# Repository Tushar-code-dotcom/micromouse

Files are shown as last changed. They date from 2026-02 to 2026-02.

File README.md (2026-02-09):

# micromouse

This repository consists of my PCB design of the micromouse robot. 
You can see the schematic and the layout pdf for quick glance.

To download the kicad files navigate to `schematic-layout-files` directory.

The micromouse is one of the oldest robotics race.
The goal is simple: get to the end of the maze as fast as possible.

This is actually my first prototype PCB for the robot, At the time of writing- I have soldered the components, including the buck converter SMPS circuit. I am using a 12V battery to power the robot. The buck converter circuit did not work, one of the possible cause- according to my limited knowledge right now, could be the use of 470uF aluminum capacitor as opposed to the recommended 680-2000uF aluminum capacitor.

The datasheet had recommened that the output capacitor can be between 100uF to 470uF if it is a tantalum capacitor.
If an aluminium capacitor were to be chosen, it had to be in between 680uF-2000uF.
According to the datasheet, 
```
Tantalum capacitors can have a very low ESR, and must be carefully evaluated if it is the only output capacitor
```
And the ESR matters, because 

```
Output Ripple Voltage = (∆IIND) (ESR of COUT) 
```
Lesser the ESR of the output capacitor, lesser would be output ripple voltage, stabler would be the output
Further analysis must be carried out to analyze the fault and determine what is the cause of no output at the buck circuit.

Components used in the micromouse are-

<table><thead>
  <tr>
    <th>STM32F407VGT6</th>
    <th>Main microcontroller</th>
  </tr></thead>
<tbody>
  <tr>
    <td>N20 600 RPM Micro-Metal gear motor</td>
    <td>Motor for driving the robot</td>
  </tr>
  <tr>
    <td>LM2576 5V Output SMPS Switcher IC- HTC   Korea</td>
    <td>Stepping down voltage from 12V to 5V</td>
  </tr>
  <tr>
    <td>AMS 1117 3.3V LDO</td>
    <td>Stepping down voltage from 12V to 5V</td>
  </tr>
  <tr>
    <td>HM-BT4502 bluetooth module</td>
    <td>For wirelessly receiving data from the uC</td>
  </tr>
  <tr>
    <td>IR   Emitter/Receiver pair(could be replaced with more accurate and cheaper mmWave   radar)</td>
    <td>For sensing the distance from the walls</td>
  </tr>
  <tr>
    <td>12V Li-ion battery</td>
    <td>For powering the robot</td>
  </tr>
</tbody>
</table>

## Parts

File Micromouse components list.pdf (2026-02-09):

# Micromouse components list

1. H bridge- https://evelta.com/h-bridge-motor-driver-ic-1.5a-sop-8/ H bridge motor driver IC SOP-8 Datasheet- https://evelta.com/content/datasheets/359-BL5612.pdf
2. Motor- # GA12-N20 12V 1000RPM Micro DC Metal Gear Reduction Motorhttps://zbotic.in/product/ga12-n20-12v-1000rpm-micro-dc-metal-gear-reduction-motor/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 (https://zbotic.in/product/ga12-n20-12v-1000rpm-micro-dc-metal-gear-reduction-motor/?gad_source=1) datasheet-
3. Motor with encoder 500 rpm gear ratio 30:1 rated current 40mA, stall current 1A--https://robokits.co.in/motors/n20-metal-gear-micro-motors/n20-metal-gear-encodermotor/ga12-n20-6v-500-rpm-all-metal-gear-micro-dc-encoder-motor-with-precious-metalbr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
srsltid=AfmBOop46_ggaORufaxEpk0p9WgjGFxgG4g6K782mz7oQ7eS4OKStQTLCls&gQT =2 (https://robokits.co.in/motors/n20-metal-gear-micro-motors/n20-metal-gear-encoder-motor/ga12-n20-6v-500-rpm-all-metal-gear-micro-dc-encoder-motor-with-precious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)
4. https://robu.in/product/ir-receiver-diode-tsop38238/?gQT=1 receiver
5. IR Emitter datasheet- https://cdn-shop.adafruit.com/datasheets/IR333_A_datasheet.pdf
6. TCRT5000 IR EMITTER/RECEIVER PAIR- https://robu.in/wp-content/uploads/2022/09/Vishay-TCRT5000L-datasheet.pdf (https://robu.in/wp-content/uploads/2022/09/Vishay-TCRT5000L-datasheet.pdf)
7. 3 way Dipswitch- https://evelta.com/dip-switch-3-way-slide-type-red-ds-03r/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 (https://evelta.com/dip-switch-3-way-slide-type-red-ds-03r/?gad_source=1) Datasheet- https://evelta.com/content/datasheets/408-DS-Series.pdf
8. Pushbutton- https://sharvielectronics.com/product/tactile-push-button-switch-12x12x7-3mm/
9. motor for propeller- https://robu.in/product/65mm-blade-propeller-prop-8520-cw-ccwcoreless-brushed-motor-indoor-racing-drone-quad-copter/ (https://robu.in/product/65mm-blade-propeller-prop-8520-cw-ccw-coreless-brushed-motor-indoor-racing-drone-quad-copter/) (3.7V)
10. 12V battery- https://quartzcomponents.com/products/12v-1200mah-rechargeable-lithiumbattery-with-warranty-for-gps-cctv-industial-and-commercial-application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¤cy=INR&utm_medium=product_sync&utm_source=google&utm_content=sag_organic&utm_campaign=sag_organic?utm_source=google&utm_medium=FreeListings&gad_source=1&gclid=Cj0KCQiAhbi8BhDI ARIsAJLOlud7CVXVUGHuGk0HCnHtH1EE9qVLhCeel78XtQ66bBOLSDcrkV2ftdoaAkUKE ALw_wcB (https://quartzcomponents.com/products/12v-1200mah-rechargeable-lithium-battery-with-warranty-for-gps-cctv-industial-and-commercial-application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)
11. 2.4V 1000RPM (30mA to 60mA continuous current) DC motor with encderhttps://robu.in/product/n12-2-4v-1200rpm-metal-gear-motor-with-encoder/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 (https://robu.in/product/n12-2-4v-1200rpm-metal-gear-motor-with-encoder/?gad_source=1)

12. If 12V motor used, then motor driver- https://evelta.com/content/datasheets/035-DRV8212PDSGR.pdf (https://evelta.com/content/datasheets/035-DRV8212PDSGR.pdf)
13. 5V 1000rpm motor- https://robu.in/product/n12-5v-1200rpm-metal-gear-motor-with-encoder/datsheet- https://robu.in/wp-content/uploads/2023/09/9-GM12-N20VA.pdf
14. propellers- https://robu.in/product/orange-hd-1209-31mm-pc-4-blade-0-8mm-propellers-4cw4ccw-clear-gray/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 (https://robu.in/product/orange-hd-1209-31mm-pc-4-blade-0-8mm-propellers-4cw4ccw-clear-gray/?gad_source=1) alternative linkhttps://evelta.com/gemfan-31mm-1209-4-blade-propeller-1-5mm/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 (https://evelta.com/gemfan-31mm-1209-4-blade-propeller-1-5mm/?gad_source=1)
15. stm32f401ret6 micrcontroller LQFP64- https://robu.in/product/stm32f401ret6-stmicroelectronics-arm-mcu-dynamic-efficiency-line-stm32-family-stm32f4-seriesmicrocontrollers-arm-cortex-m4/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 (https://robu.in/product/stm32f401ret6-stmicroelectronics-arm-mcu-dynamic-efficiency-line-stm32-family-stm32f4-series-microcontrollers-arm-cortex-m4/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)
16.

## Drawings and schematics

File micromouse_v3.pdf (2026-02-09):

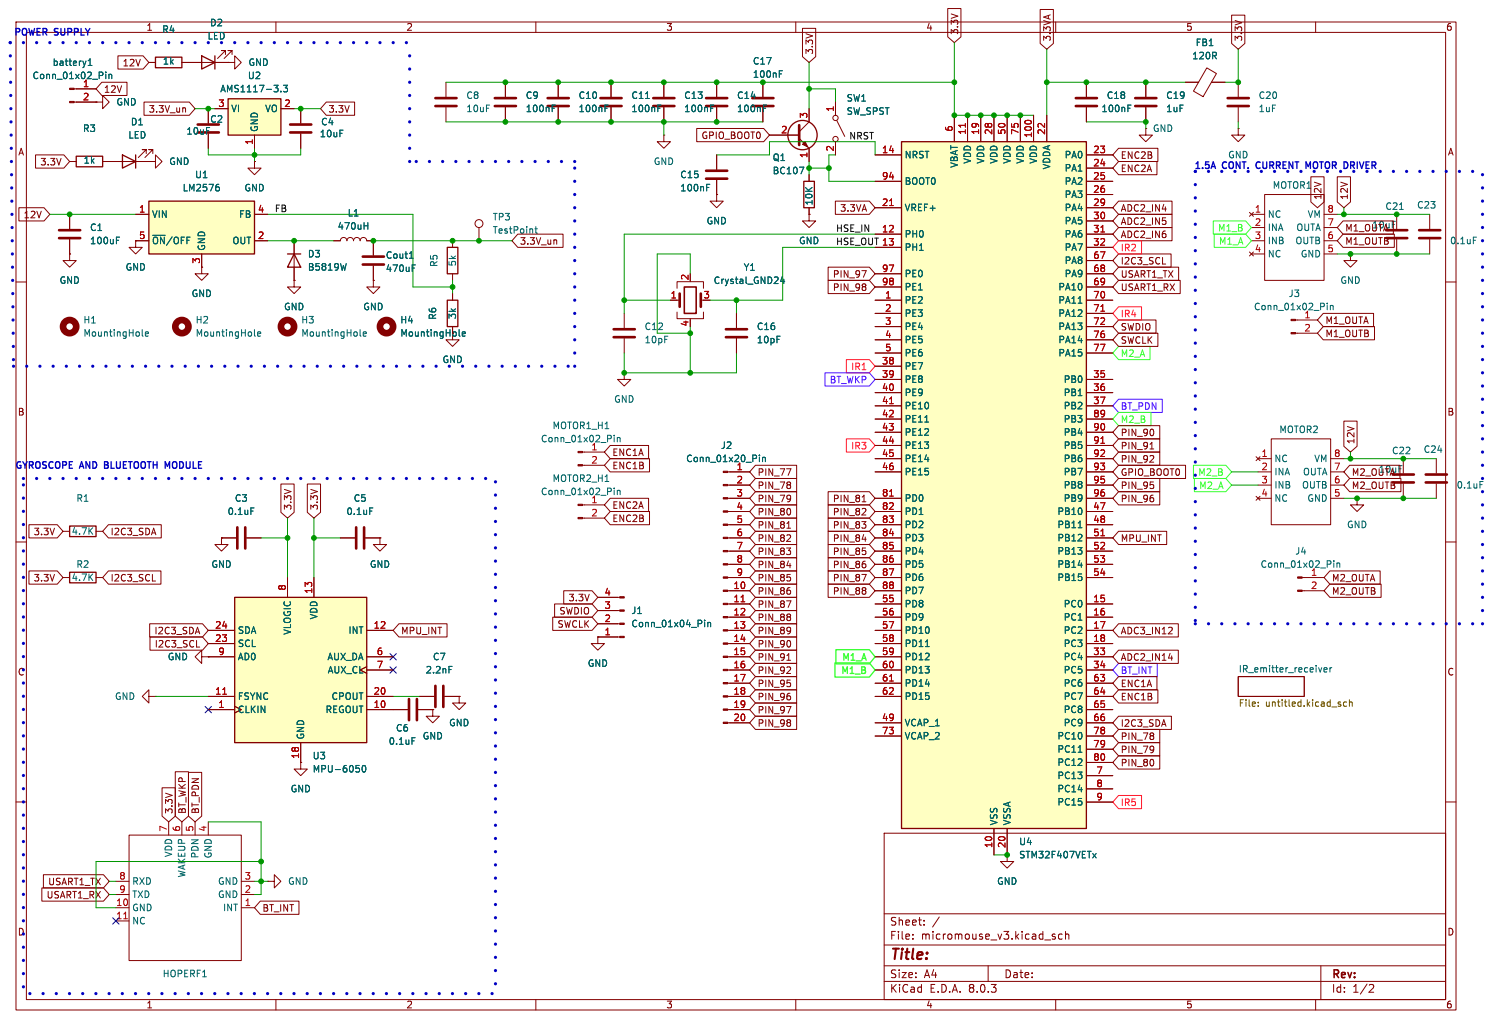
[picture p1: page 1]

3 FB 4 ~{ON}/OFF 5 U2 AMS1117-3.3 GND

1.5A CONT. CURRENT MOTOR DRIVER GYROSCOPE AND BLUETOOTH MODULE

Id: 1/2 Title: File: micromouse_v3.kicad_sch Sheet: /

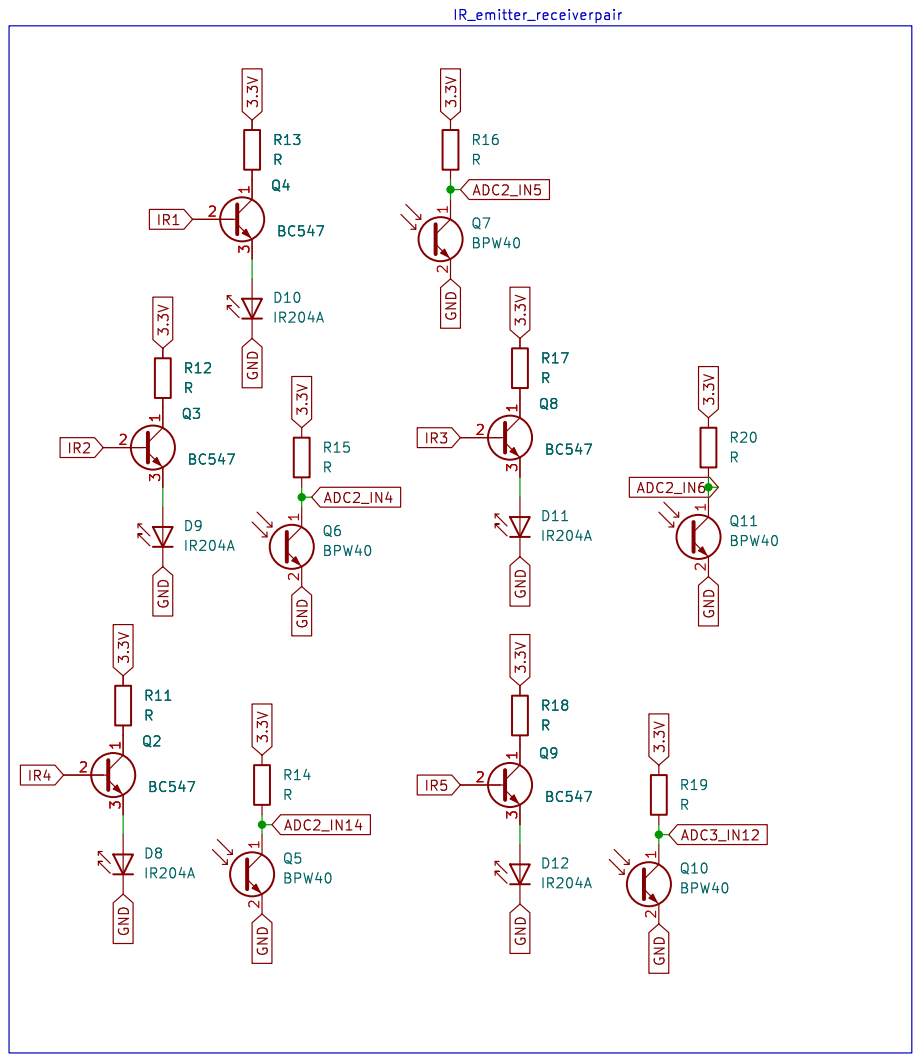
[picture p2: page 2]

Id: 2/2 Title: File: untitled.kicad_sch Sheet: /IR_emitter_receiver/ R14 R

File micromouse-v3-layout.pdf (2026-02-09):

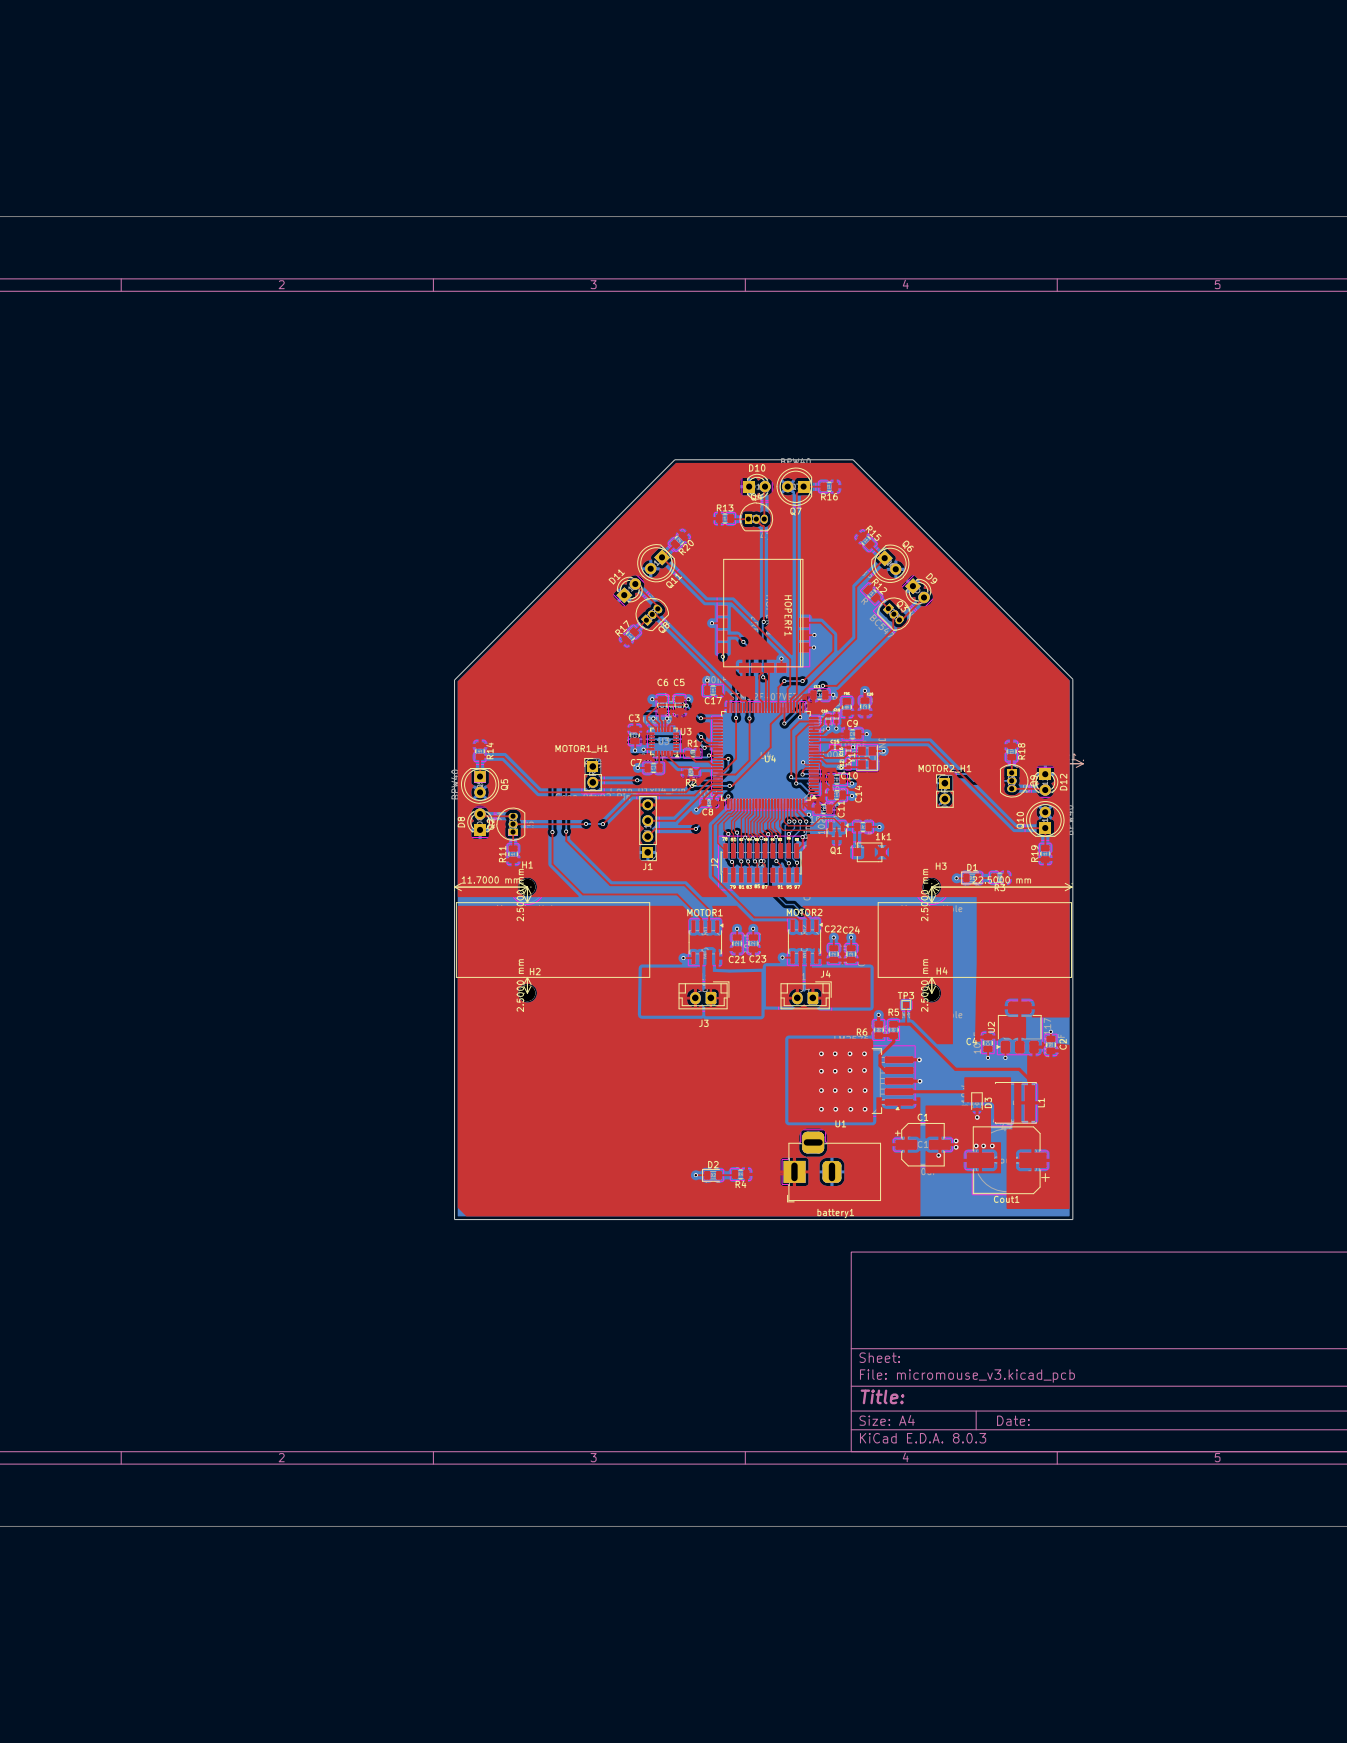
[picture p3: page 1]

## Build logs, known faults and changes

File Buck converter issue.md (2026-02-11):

I am not sure which of these issue could be the root cause of my DC-DC step down converter not working so I will list them one by one

### 1. Soldering at a higher temperature

I have soldered the buck converter, with a hot air gun at a temperature of 350 degree celsius for roughly 30 seconds-1 minute, I have resorted to such high temperatures, because a considerable amount of solder had to be melted before placing the IC on the PCB

![[Pasted image 20260210220326.png]]

![[WhatsApp Image 2026-02-10 at 10.07.25 PM.jpeg]]

#### **The issue**
Maybe the exposure to such temperature(350 deg C) could have caused the IC, to not work at all, because I was getting no input at the feedback pin

![[Pasted image 20260210225434.png]]
### 2. Using LTSpice model of TI instead of HTC korea to simulate
Maybe this is a bigger blunder considering that I have bought an HTC LM2576 regulator and am uisng the TI LTSpice model(due to lack of response of HTCKorea to send the model).

I thought the general characteristics would be the same, and maybe there would be a few slight variations in the ripple current
### 3. I have not tested the IC before soldering

I did not do any sort of time domain analysis, as I do not know how to build the test circuit, nor is there any test circuit provided by HTC Korea, TI has a thorough documentation on how to test their LM2576, but again since they are different companies, I didn't want to do that.

### 4. Did not follow the recommended output capacitor value

	I know this is a big issue, in terms of output ripple voltage but, since there was little to no output voltage on the AMS1117 3.3V IC, I had used an NI-DAQ to measure the output votlage but I was not able to get any value

### 5. RMS ripple current rating of the input capacitor

I have used a 100uF input capacitor  as recomendded by the datasheet
The datasheet recommends the RMS ripple current rating of the capacitor to be greater than `1.2 × (tON/T) × ILOAD` . I have not looked into ripple current rating of the capacitor

```
RMS ripple current= 1.2 × (tON/T) × ILOAD where 
tON/T = VOUT/VIN for a buck regulator
```
I selected the catch diode properly with a reverse voltage rating of 1.2 times greater than the maximum load current.
